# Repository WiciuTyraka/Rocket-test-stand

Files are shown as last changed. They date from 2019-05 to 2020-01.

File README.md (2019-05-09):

# Rocket test stand

## About
This is a project of rocket test stand to measure the trust and temperature of the engine and to save the data on SD-card. In nearly future I will add a wireless communication with computer to collect and proces data in real time. To wireless communication i will use a LoRa module.

- [Rocket test stand](#rocket-test-stand)
  * [About](#about)
  *  [PCB](#pcb)
      - [Schema](#schema)
      - [Board](#board)
      - [Libraries](#libraries)
  * [Sensors](#sensors)
      - [SD-card](#sd-card)
      - [Load cell and HX711](#load-cell-and-hx711)
      - [Thermocouples and max6675](#thermocouples-and-max6675)
      - [LoRa module](#lora-module)
      - [Pin map](#pin-map)
  * [Code for arduino](#code-for-arduino)
  * [Code for STM32](#code-for-stm32)

## PCB
Circut board is designed in Eagle

### Schema
 Rocket test stend consist of two board.
 - First board is a shield for Arduino Uno or STM32 Nucelo board. On this board is located a adpter for SD-card, amplifire for load cell and thermometr, and also a LoRa module.<br/>
[schema of rocket test stand board](https://github.com/WiciuTyraka/Rocket-test-stand/blob/master/PCB/Schema/Rocekt_test_stand.sch)
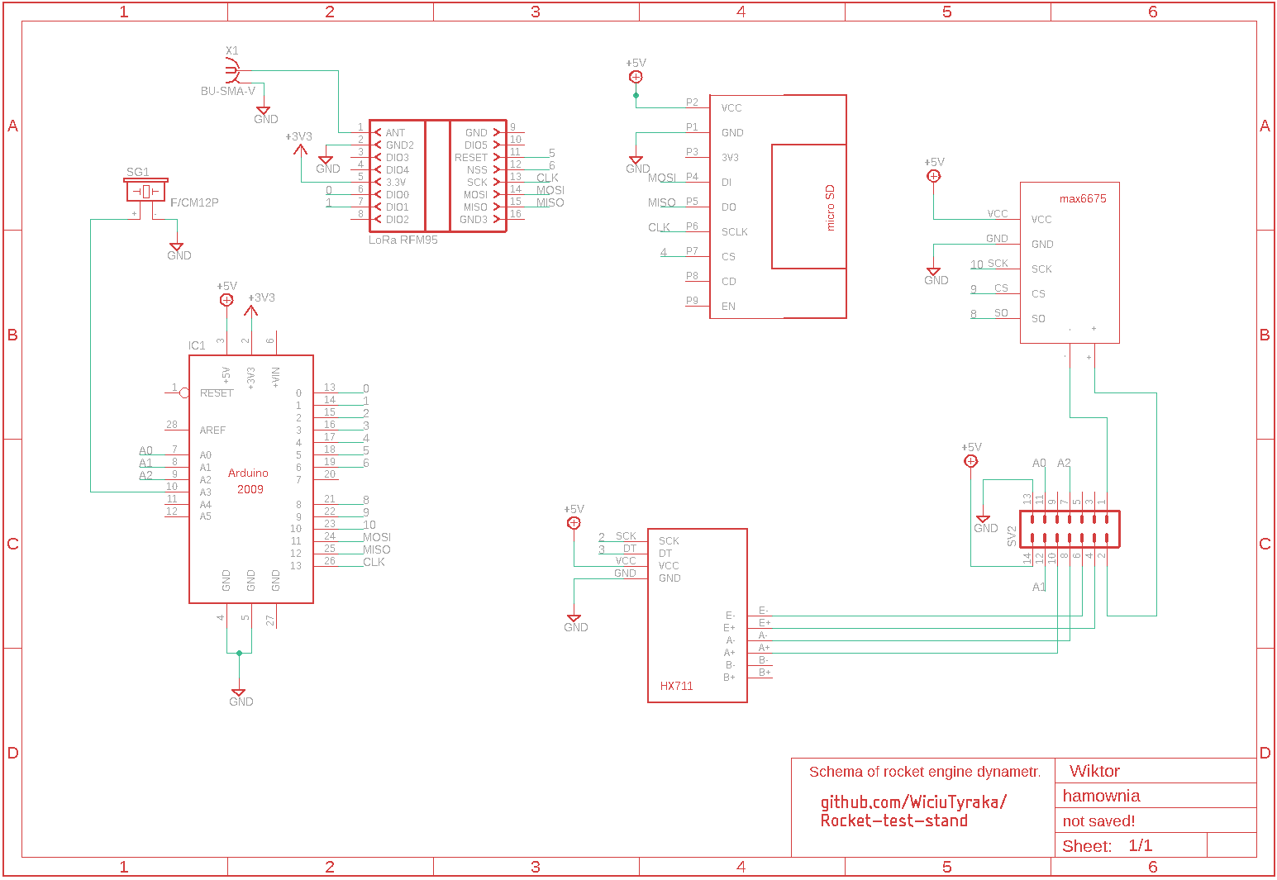
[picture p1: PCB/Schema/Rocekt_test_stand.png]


- Second board is used to collecting signals from sensors and ignite the engine.<br/>
[schema of input rocket test stand board](https://github.com/WiciuTyraka/Rocket-test-stand/blob/master/PCB/Schema/Rocekt_test_stand_input.sch)
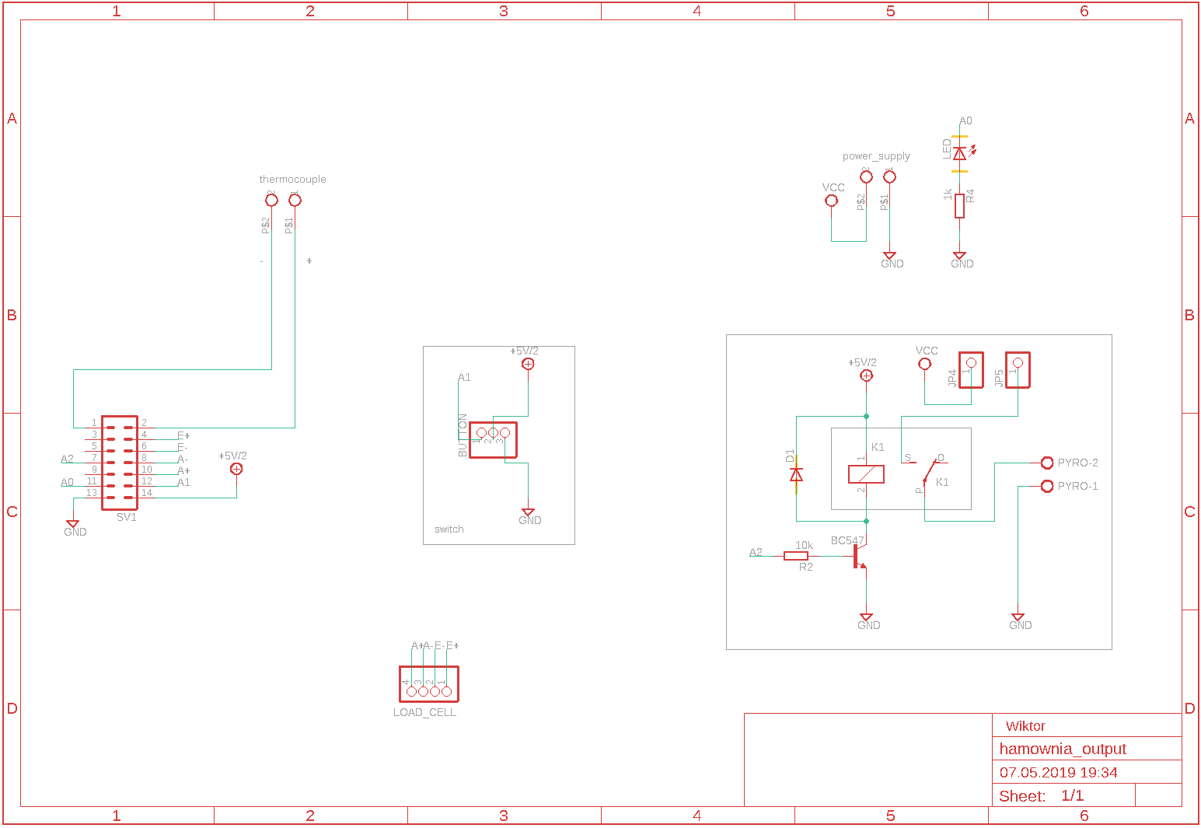
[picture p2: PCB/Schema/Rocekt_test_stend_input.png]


### Board
links for downloading a board file.
- [link for rocket_test_stend.brd](https://github.com/WiciuTyraka/Rocket-test-stand/blob/master/PCB/Board/Rocekt_test_stand.brd)
- [link for rocket_test_stend_input.brd](https://github.com/WiciuTyraka/Rocket-test-stand/blob/master/PCB/Board/Rocekt_test_stand_input.brd)

### Libraries
Here are a necessary libraries for elements thats are used in project.
- [ark 8.5mm](https://github.com/WiciuTyraka/Rocket-test-stand/blob/master/PCB/Lib/111_ark_8.5mm.lbr)
- [hx711](https://github.com/WiciuTyraka/Rocket-test-stand/blob/master/PCB/Lib/111_hx711.lbr)
- [LoRa module](https://github.com/WiciuTyraka/Rocket-test-stand/blob/master/PCB/Lib/111_LORA.lbr)
- [max6675](https://github.com/WiciuTyraka/Rocket-test-stand/blob/master/PCB/Lib/111_max6675.lbr)
- [microsd](https://github.com/WiciuTyraka/Rocket-test-stand/blob/master/PCB/Lib/111_microsd.lbr)

## Sensors
In this project are used few sensors and device, here you can find a exemple code, libraries and datasheet for them.

### SD-card
---
Micro sd-card adapter is used for saving all data in txt file or as a json.
<details>
<summary>details</summary>
</br>

#### Wireing schema
This is the schema for all the wireing with arduino
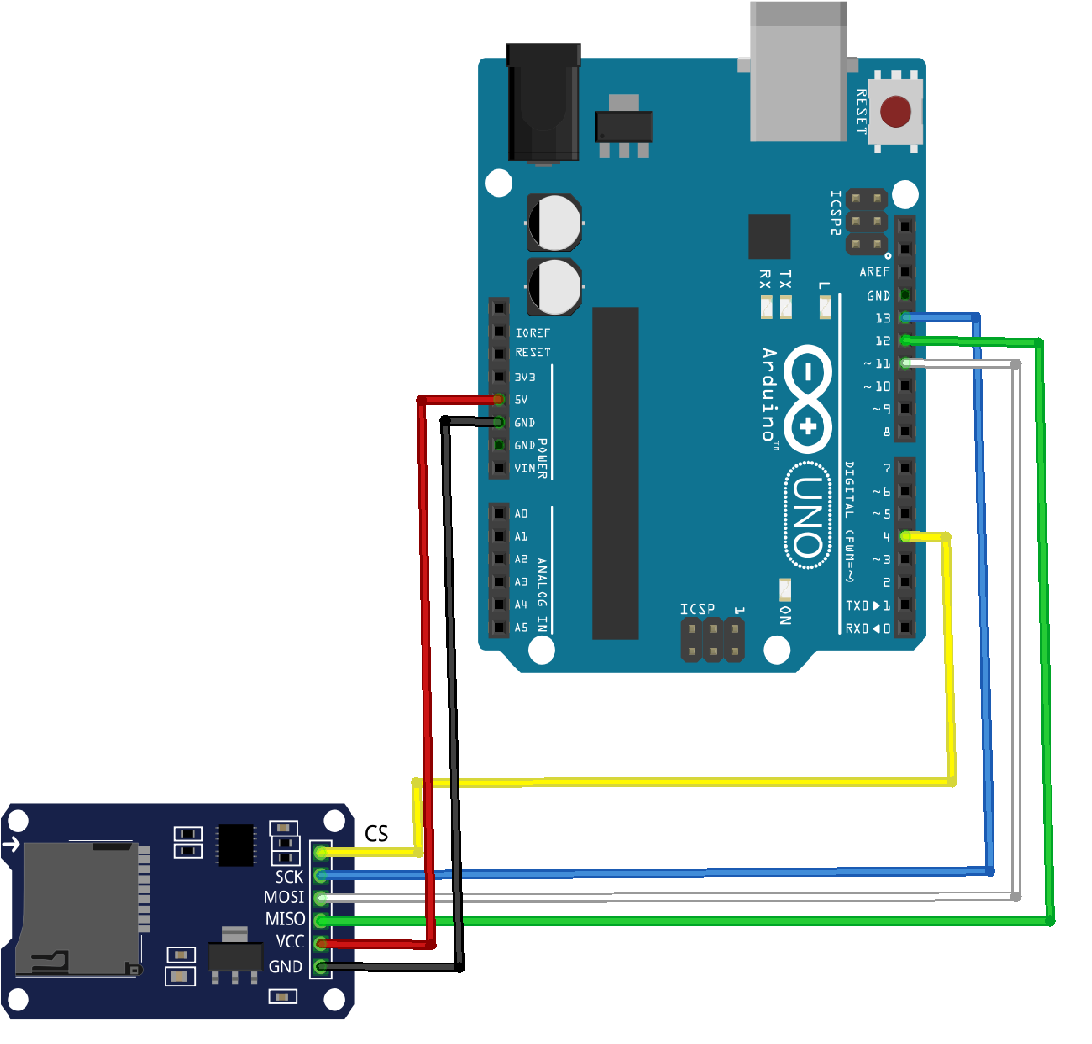
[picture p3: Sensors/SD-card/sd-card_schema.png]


#### Adapter wireing
| MicroSD Card Adapter | Adruino UNO Pin |
|---|---:|
| CS | 4 |
| SCK | 13 |
| MOSI | 11 |
| MISO | 12 |
| VCC | 5V |
| GND | GND |

#### Arduino code
[the necessary code is here](https://github.com/WiciuTyraka/Rocket-test-stand/blob/master/Sensors/SD-card/save_to_file/save_to_file.ino)
</details>

### Load cell and HX711
---
Load cell id used for measuring a engine thrust. Analog signal form load cell is converting to digital by HX711 amplifier
<details>
<summary>details</summary>
</br>
I cant find a datasheet for my chinese load cell so made this table

#### Basic load resistance checks
| Resistance check | Typical 350 Ω |
|---|---:|
| Ex+ to Ex- | ~410Ω |
| S+ to S- | 350Ω |
| Ex+ to S+ | ~315Ω |
| Ex+ to S- | ~315Ω |
| Ex- to S+ | ~280Ω |
| Ex- to S- | ~280Ω |

#### Load cell wireing
| HX711 | Load cell |
|---|---:|
| E+ | white |
| E- | red |
| S+ | black |
| S- | green |

#### Amplifer schema
This is a schema for all the wireing with arduino
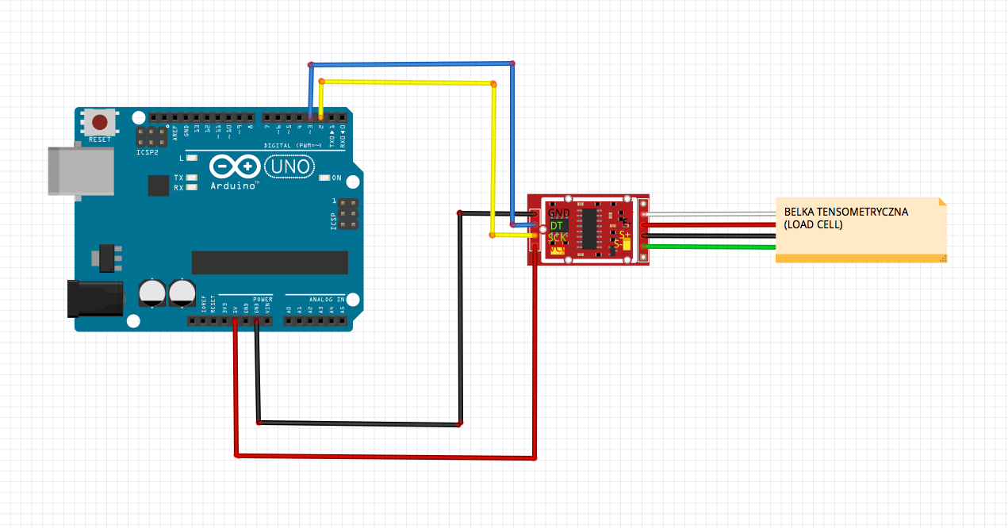
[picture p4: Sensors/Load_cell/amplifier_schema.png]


#### HX711 library
You can download the necessary library here:
[download](https://halckemy.s3.amazonaws.com/uploads/attachments/392655/HX711-master.zip)

#### Arduino code
All the code necessary for calibration the load cell and measuring the force:
- calibration:
[the code is here](https://github.com/WiciuTyraka/Rocket-test-stand/blob/master/Sensors/Load_cell/calibration/calibration.ino)
- measurment:
[the code is here](https://github.com/WiciuTyraka/Rocket-test-stand/blob/master/Sensors/Load_cell/measurment/measurment.ino)

#### Datasheet
[link](https://circuits4you.com/wp-content/uploads/2016/11/hx711_datasheet_english.pdf)
</details>

### Thermocouples and max6675
---
To measure a temperature of the combustion chember and nozzle I'm using a thermocouple. Analog signal from this sensor is converting to digital by max6675 amplifier

<details>
<summary>details</summary>
</br>

#### Specifications of max6675
| | |
|---|---:|
| Suply Voltage | 3.3 to 5 VDC |
| Operating Current | ~50mA |
| Measurement Range | 0 - 1024^∘C |
| Measurement Resolution | +/- 0.25^∘C |
| Output | Uses SPI interface |
| Required sensor | K Thermocouple |

#### Thermocouples schema
This is the schema for all the wireing with arduino
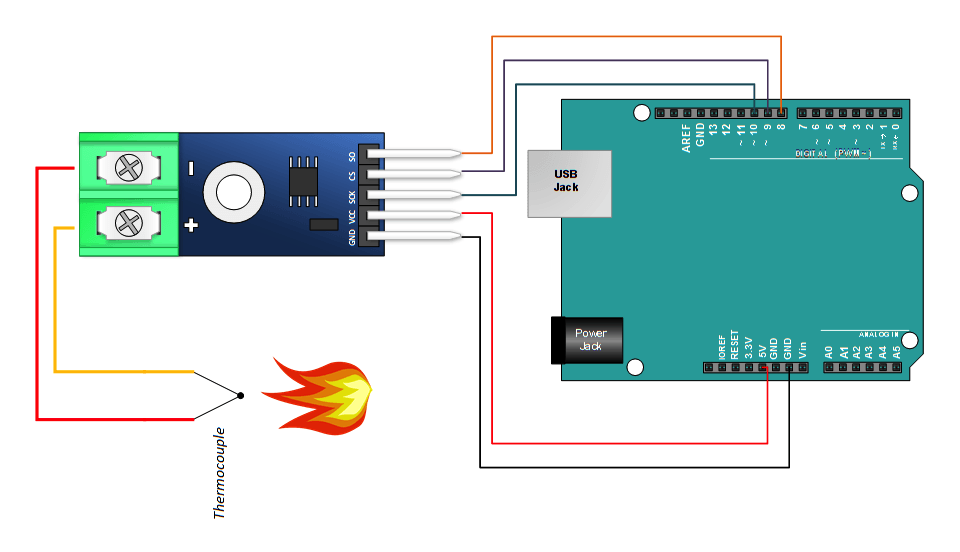
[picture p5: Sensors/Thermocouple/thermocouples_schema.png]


#### MAX6675 library
You can download the necessary library here:
[download](https://github.com/adafruit/MAX6675-library)

#### Arduino code
Basic code for reading temperature
[the necessary code is here](https://github.com/WiciuTyraka/Rocket-test-stand/blob/master/Sensors/Thermocouple/thermocouples/thermocouples.ino)

#### Datasheet
[link](http://henrysbench.capnfatz.com/wp-content/uploads/2015/05/MAX6675-Datasheet.pdf)

</details>

### LoRa module
---
I used LoRa transceiver to ignite the engine from safe distance also wireless communication allows me to watch data in real time.

<details>
<summary>details</summary>
</br>

The chip I used in project is a RFM95W transceiver.
The  RFM95W transceivers  feature  the  LoRaTM  long range modem that provides ultra-long range spread spectrum communication and high interference immunity whilst minimising current consumption.

#### RFM95W schema
This is the schema for all the wireing with arduino
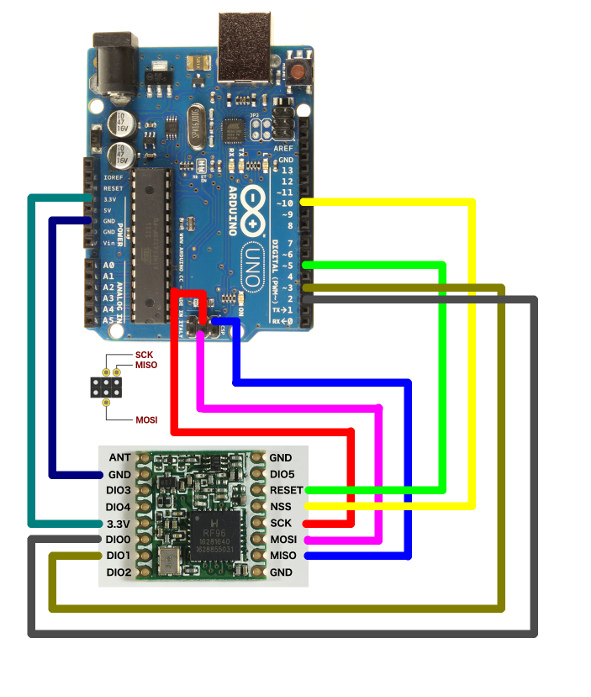
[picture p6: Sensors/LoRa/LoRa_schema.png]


#### RFM95W library
You can download the necessary library here:
[download](https://github.com/PaulStoffregen/RadioHead)

#### Arduino code
Here is a code for a transmiter and reciver(in fact both of them are transceivers) :
- transmiter:
[the code is here](https://github.com/WiciuTyraka/Rocket-test-stand/blob/master/Sensors/LoRa/transmiter/transmiter.ino)
- reciver:
[the code is here](https://github.com/WiciuTyraka/Rocket-test-stand/blob/master/Sensors/LoRa/reciver/reciver.ino)

#### Datasheet
[link](https://www.hoperf.com/modules/lora/RFM95.html)

</details>

### Pin map
---
This table contains information abaout all pins to witch are connected device

| Pin number |Device |
|---|--- |
| 0 |LoRa DIO0  |
| 1 |LoRa DIO1  |
| 2 |HX711 CLK  |
| 3 |HX711 DOUT |
| 4 |SD card |
| 5 |LoRa RESET |
| 6 |LoRa CS |
| 8 |max6675 CS |
| 9 |max6675 SO |
| 10 |max6675 SCK|
| 11 |MOSI |
| 12 |MISO |
| 13 |CLK |
| 14 |switch |
| 15 |led |
| 16 |ignite |
| 17 |buzzer |

## Code for Arduino

This version of code not include a wireless communication
- here you can find a [code](https://github.com/WiciuTyraka/Rocket-test-stand/blob/master/Arduino_code/Rocekt_test_stand/Rocekt_test_stand.ino)

## Code for STM32
cause i'm very busy right now, i'll back to this task in nearly future.

*by* Wiktor Tasarek

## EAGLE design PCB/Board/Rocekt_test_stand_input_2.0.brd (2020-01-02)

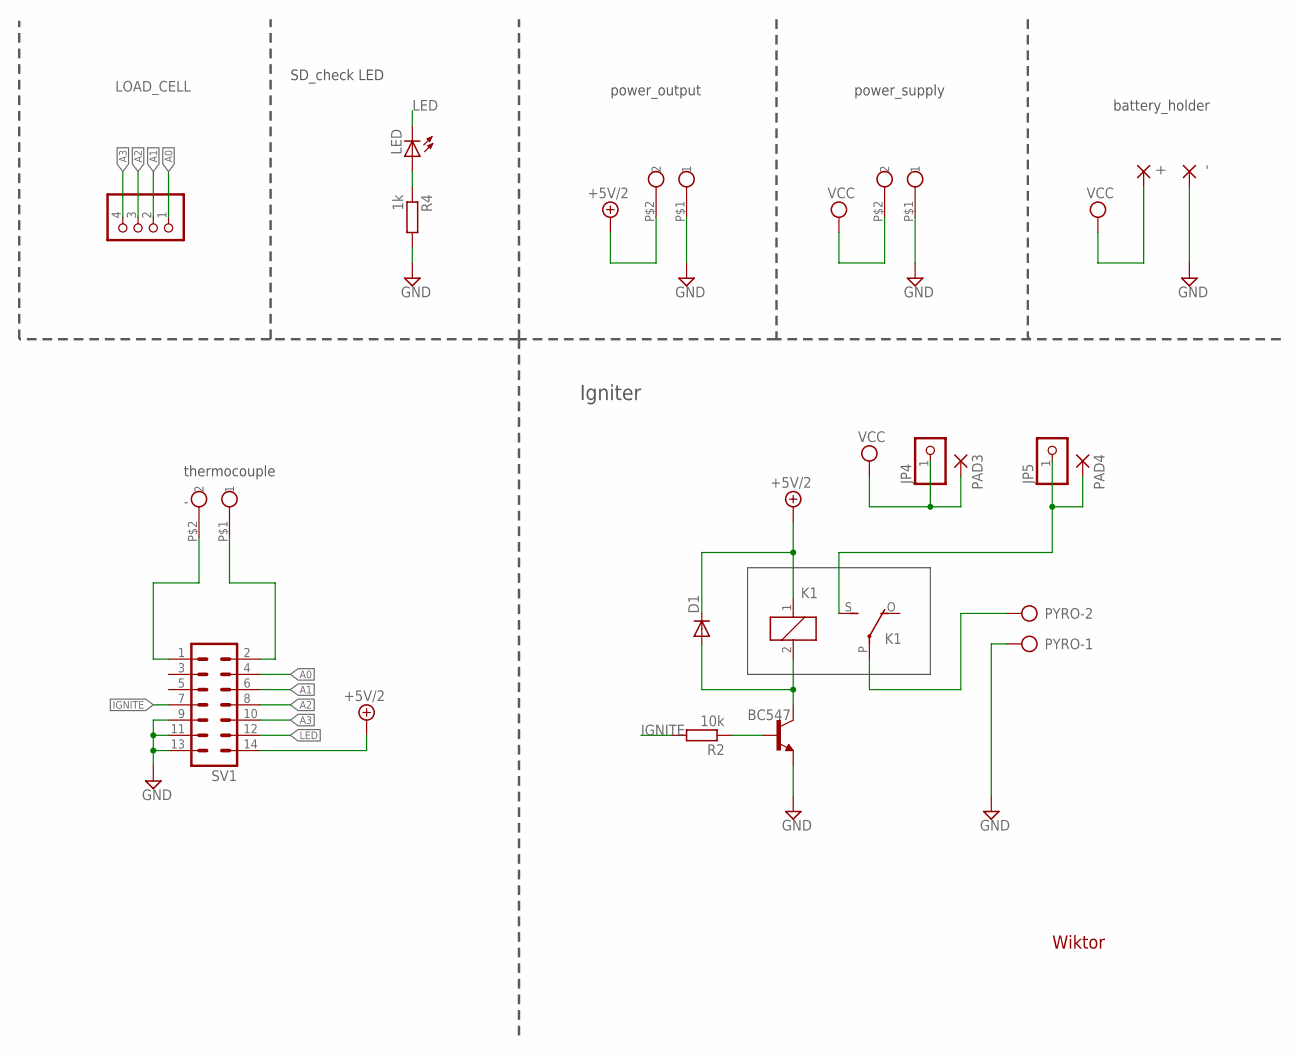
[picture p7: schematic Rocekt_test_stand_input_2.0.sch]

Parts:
+: SMD5; SMD2,54-5,08
-: SMD5; SMD2,54-5,08
D1: 1N4004; DO41-10
JP4, JP5: PINHD-1X1; 1X01
K1: G5L; G5LE
LED: LED_ELD260; LED_LD260
LOAD_CELL: PINHD-1X4; 1X04
PAD3, PAD4: SMD2; SMD1,27-2,54
POWER_SUPPLY, POWER_SUPPLY1: ARK_8.5MM; ZLACZESRUBOWE8.5MM
PYRO: AK500/2
R2: 10k; 0204/5
R4: 1k; 0204/5
SV1: ML14
T1: BC547; TO92
U$1: ARK_8.5MM; ZLACZESRUBOWE8.5MM

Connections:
+5V/2: D1.C, K1.1, POWER_SUPPLY1.P$2 (2), SV1.14
-: SV1.1, U$1.P$2 (2)
A0: LOAD_CELL.1, SV1.4
A1: LOAD_CELL.2, SV1.6
A2: LOAD_CELL.3, SV1.8
A3: LOAD_CELL.4, SV1.10
GND: -.1, POWER_SUPPLY.P$1 (1), POWER_SUPPLY1.P$1 (1), PYRO.1, R4.2, SV1.9, SV1.11, SV1.13, T1.1 (E)
IGNITE: R2.2, SV1.7
LED: LED.K (C), SV1.12
unnamed: D1.A, K1.2, T1.3 (C)
unnamed: R2.1, T1.2 (B)
unnamed: K1.P, PYRO.2
unnamed: SV1.2, U$1.P$1 (1)
unnamed: LED.A, R4.1
unnamed: JP5.1, K1.S, PAD4.1
VCC: +.1, JP4.1, PAD3.1, POWER_SUPPLY.P$2 (2)

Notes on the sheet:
thermocouple
power_supply
Wiktor
battery_holder
power_output
SD_check LED
Igniter

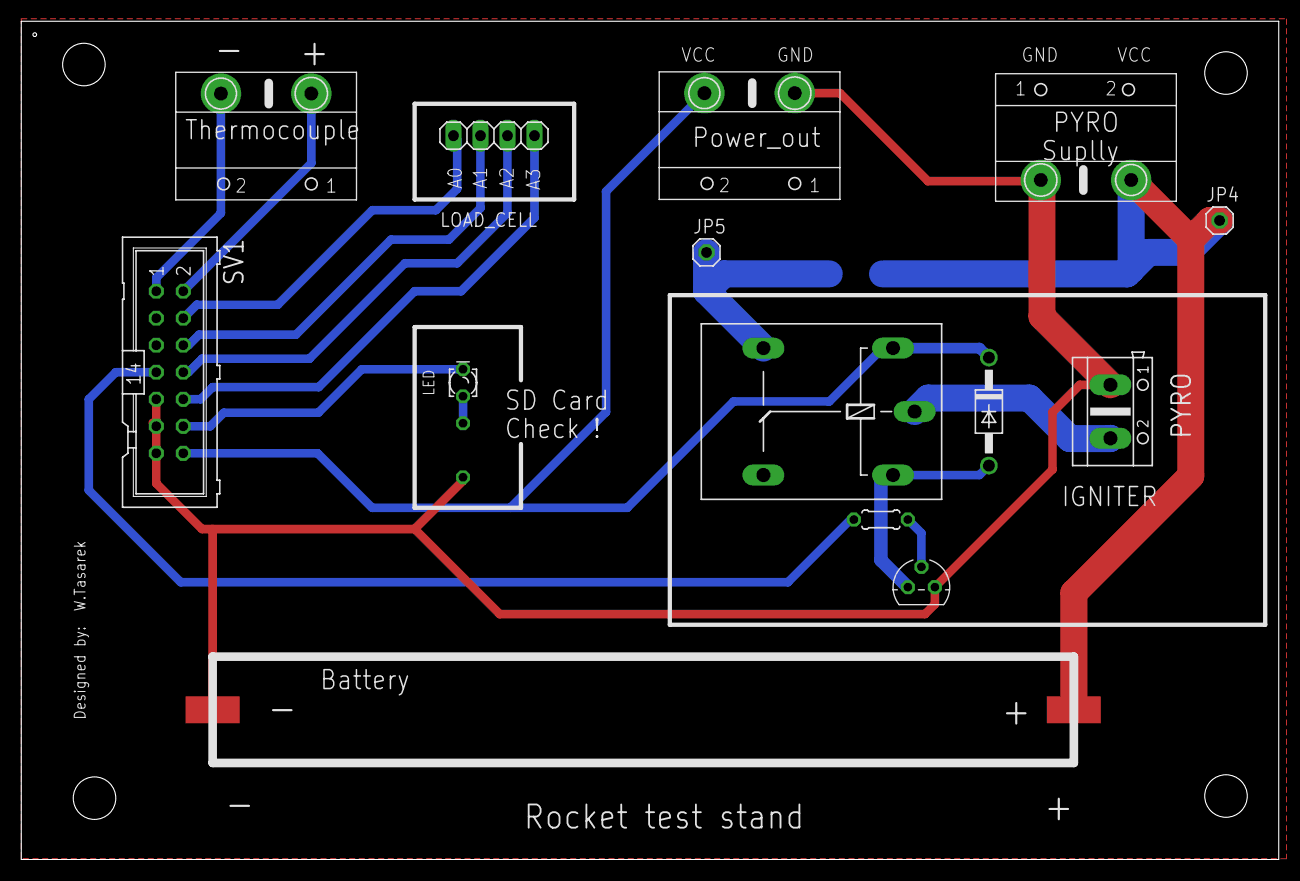
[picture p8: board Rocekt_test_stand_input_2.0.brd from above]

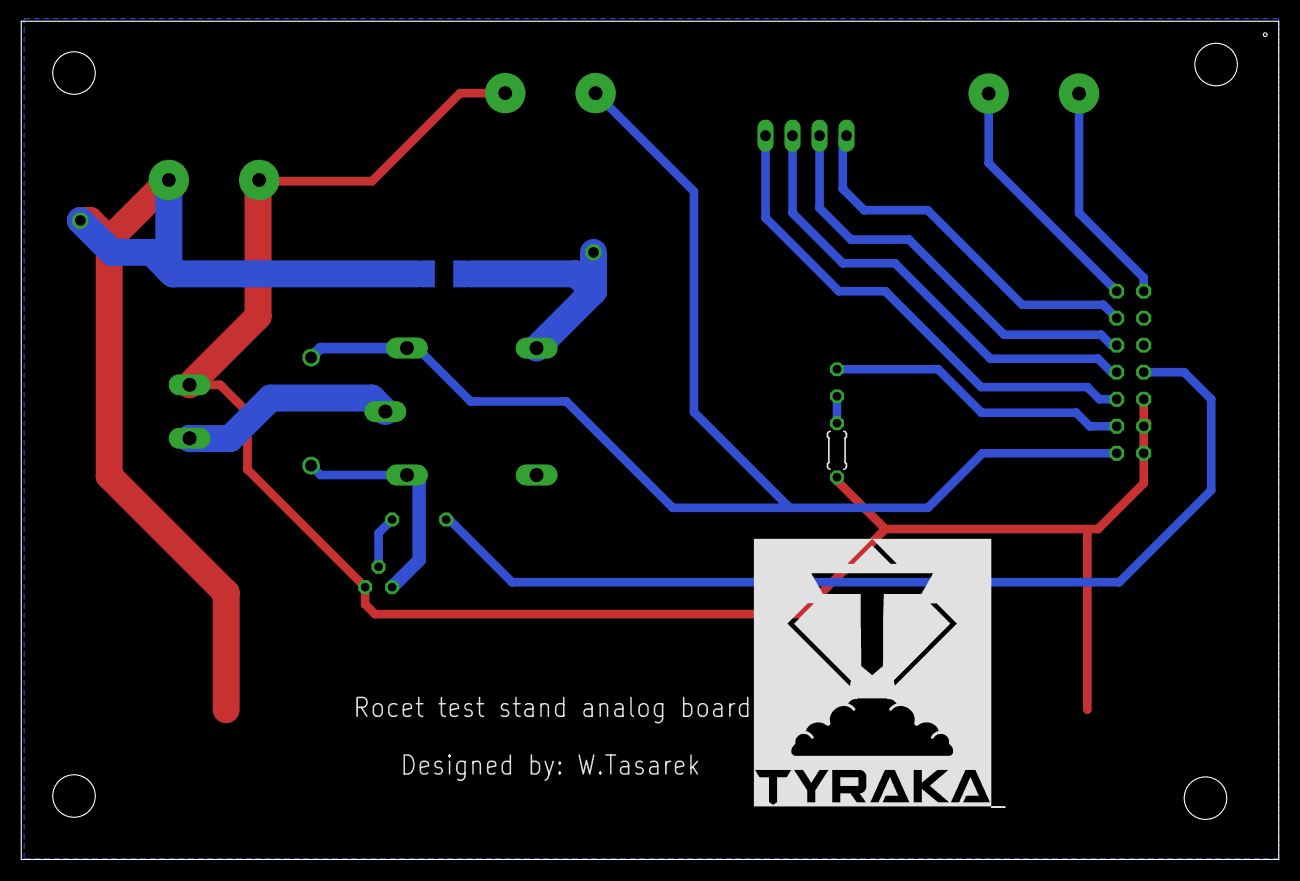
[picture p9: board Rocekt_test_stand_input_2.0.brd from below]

Board: 2 copper layers, 118.3 x 78.8 mm, 18 parts (3 on the bottom side), 16 nets.

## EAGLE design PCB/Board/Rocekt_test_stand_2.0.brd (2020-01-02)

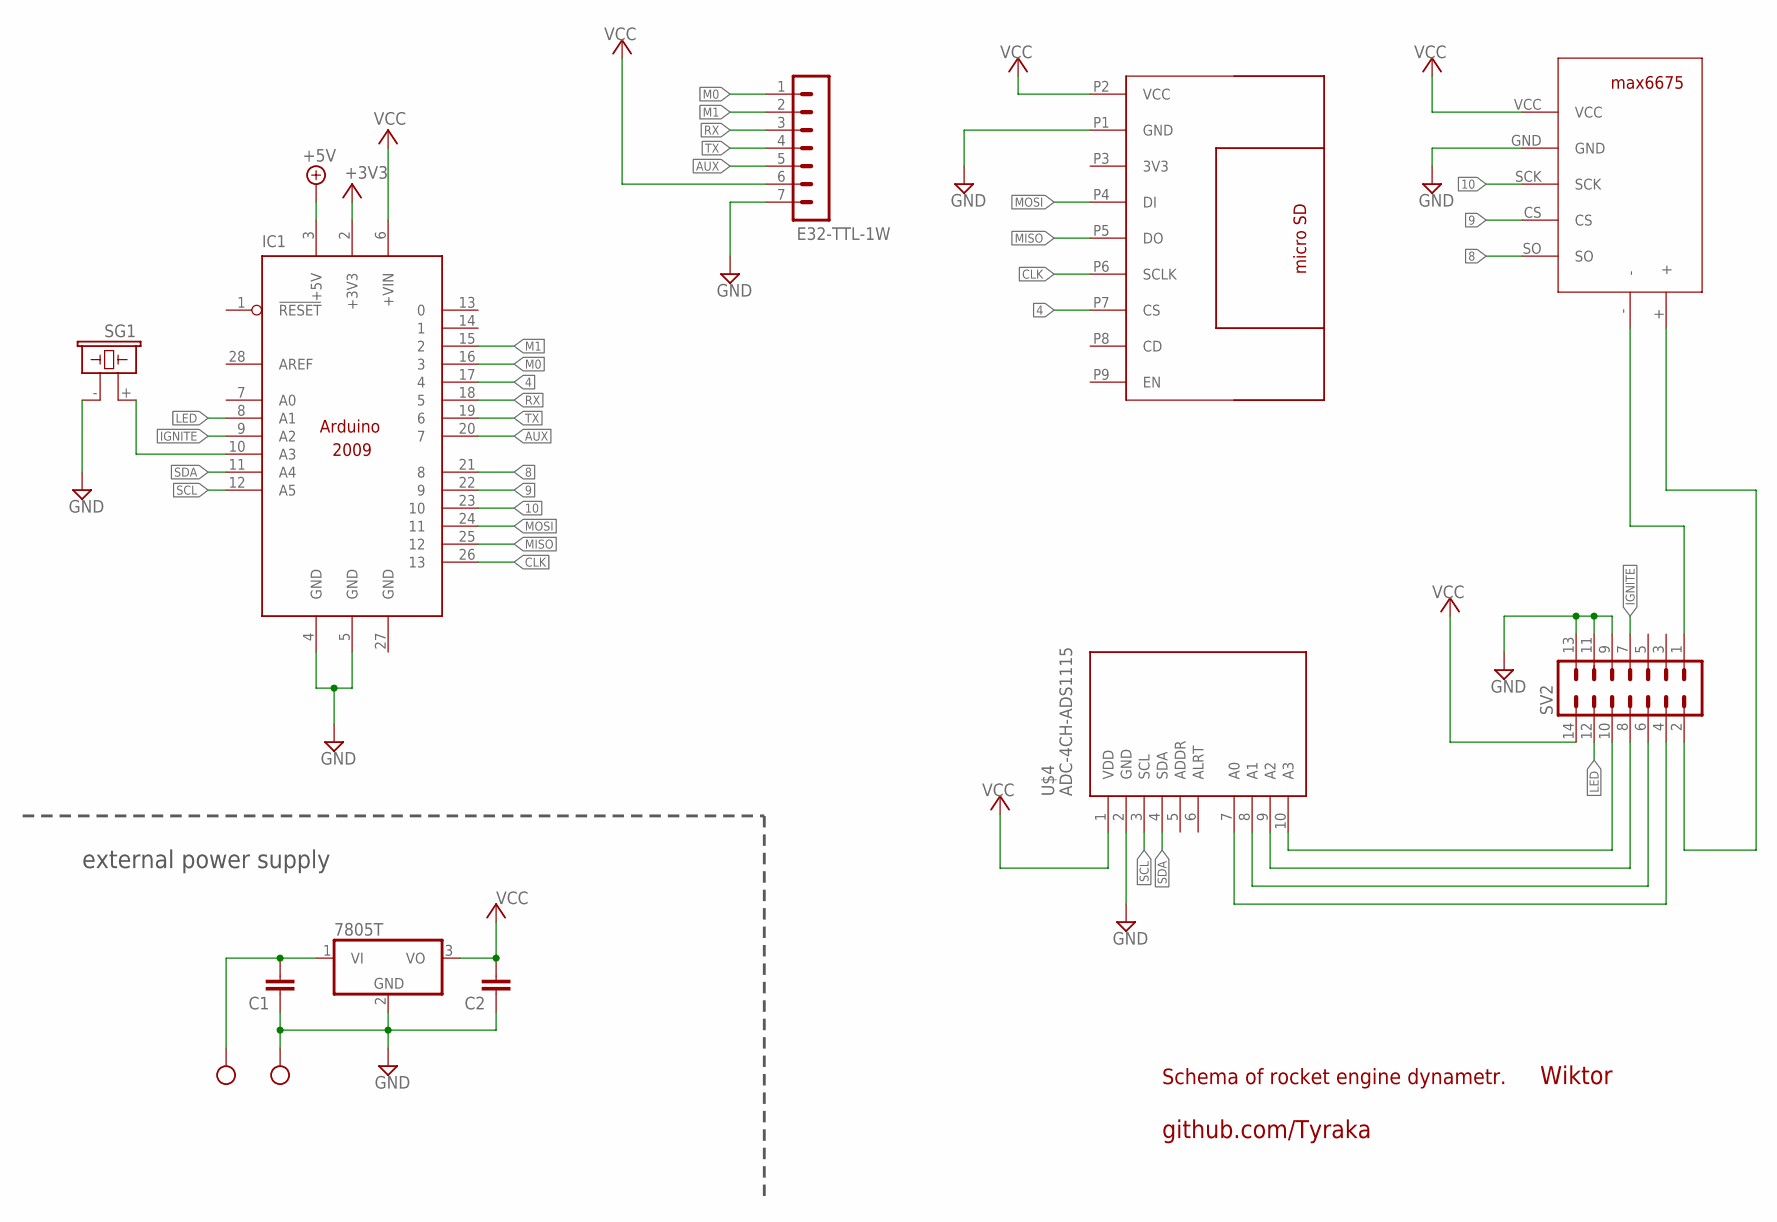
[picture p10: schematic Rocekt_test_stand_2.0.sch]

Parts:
C1, C2: C2.5/4; C2.5-4
E32-TTL-1W: MA07-1
IC1: ARDUINO2009_10; ARDUINO2009
IC2: 7805T; TO220H
SD1: MICRO_SD
SG1: F/CM12P
SV2: ML14
U$2: MAX6675; MAX6675_FOOTPRINT
U$4: ADC-4CH-ADS1115
X1: AK300/2

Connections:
4: IC1.17 (4), SD1.P7 (CS)
8: IC1.21 (8), U$2.SO
9: IC1.22 (9), U$2.CS
10: IC1.23 (10), U$2.SCK
+3V3: IC1.2 (+3V3)
+5V: IC1.3 (+5V)
AUX: E32-TTL-1W.5, IC1.20 (7)
CLK: IC1.26 (13), SD1.P6 (SCLK)
GND: C1.1, C2.1, E32-TTL-1W.7, IC1.4 (GND), IC1.5 (GND), IC1.27 (GND), IC2.2 (GND), SD1.P1 (GND), SG1.- (2), SV2.9, SV2.11, SV2.13, U$2.GND, U$4.2 (GND), X1.2
IGNITE: IC1.9 (A2), SV2.7
LED: IC1.8 (A1), SV2.12
M0: E32-TTL-1W.1, IC1.16 (3)
M1: E32-TTL-1W.2, IC1.15 (2)
MISO: IC1.25 (12), SD1.P5 (DO)
MOSI: IC1.24 (11), SD1.P4 (DI)
unnamed: SV2.2, U$2.+
unnamed: IC1.10 (A3), SG1.+ (1)
unnamed: SV2.1, U$2.-
unnamed: SV2.4, U$4.7 (A0)
unnamed: SV2.10, U$4.10 (A3)
unnamed: SV2.8, U$4.9 (A2)
unnamed: SV2.6, U$4.8 (A1)
unnamed: C1.2, IC2.1 (VI), X1.1
RX: E32-TTL-1W.3, IC1.18 (5)
SCL: IC1.12 (A5), U$4.3 (SCL)
SDA: IC1.11 (A4), U$4.4 (SDA)
TX: E32-TTL-1W.4, IC1.19 (6)
VCC: C2.2, E32-TTL-1W.6, IC1.6 (+VIN), IC2.3 (VO), SD1.P2 (VCC), SV2.14, U$2.VCC, U$4.1 (VDD)

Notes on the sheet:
Wiktor
Schema of rocket engine dynametr.
github.com/Tyraka
external power supply

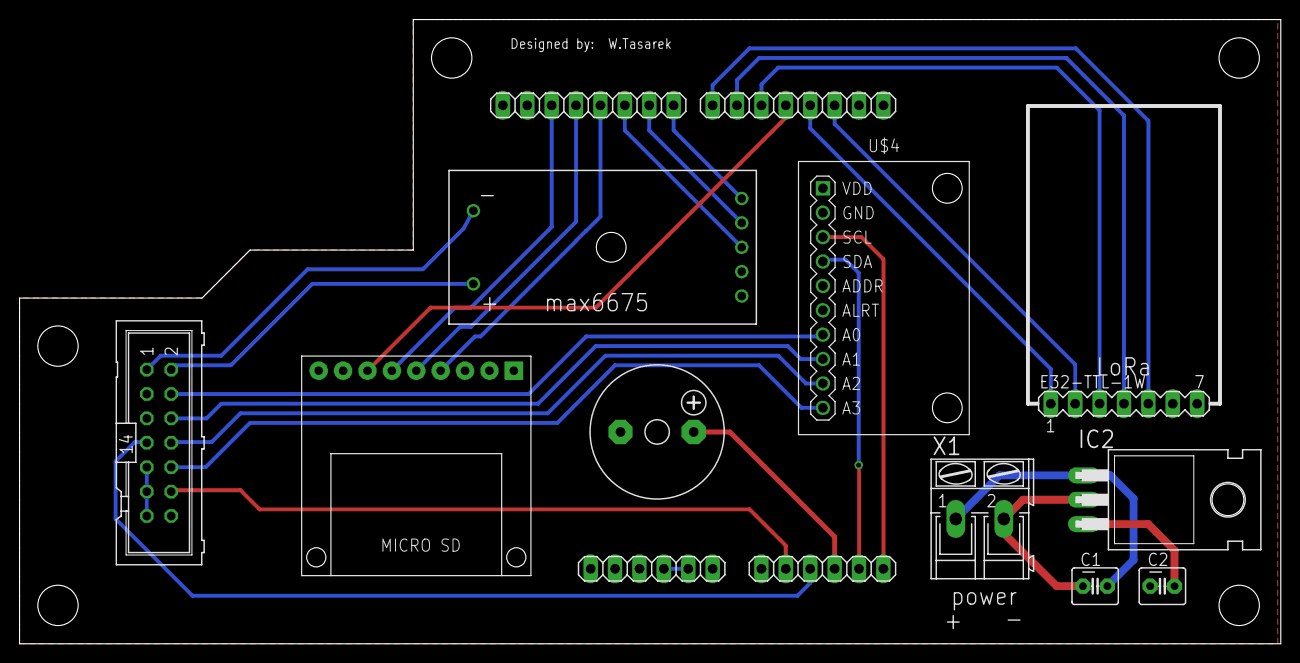
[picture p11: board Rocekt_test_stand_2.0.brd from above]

Board: 2 copper layers, 131.3 x 65.0 mm, 11 parts (0 on the bottom side), 26 nets.

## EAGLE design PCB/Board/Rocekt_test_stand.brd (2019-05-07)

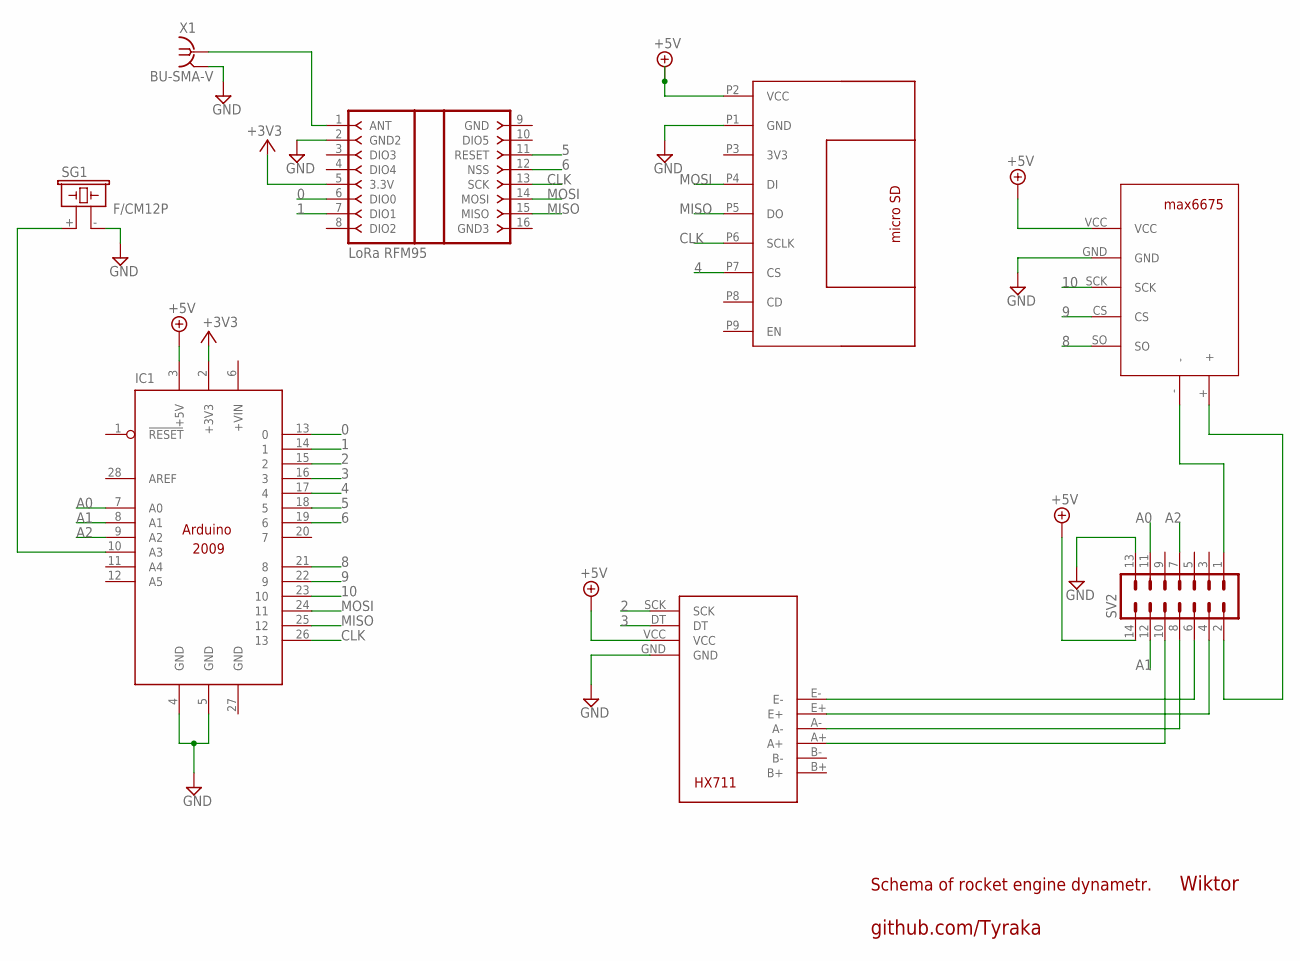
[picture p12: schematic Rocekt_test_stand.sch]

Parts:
IC1: ARDUINO2009_10; ARDUINO2009
LORA: LORA_RFM95_ADAPTERLORA_RFM95W; LORA_RFM95_ADAPTER
SD1: MICRO_SD
SG1: F/CM12P
SV2: ML14
U$1: HX711
U$2: MAX6675; MAX6675_FOOTPRINT
X1: BU-SMA-V

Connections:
0: IC1.13 (0), LORA.6 (DIO0)
1: IC1.14 (1), LORA.7 (DIO1)
2: IC1.15 (2), U$1.SCK
3: IC1.16 (3), U$1.DT
4: IC1.17 (4), SD1.P7 (CS)
5: IC1.18 (5), LORA.11 (RESET)
6: IC1.19 (6), LORA.12 (NSS)
8: IC1.21 (8), U$2.SO
9: IC1.22 (9), U$2.CS
10: IC1.23 (10), U$2.SCK
+3V3: IC1.2 (+3V3), LORA.5 (3.3V)
+5V: IC1.3 (+5V), SD1.P2 (VCC), SV2.14, U$1.VCC, U$2.VCC
A0: IC1.7 (A0), SV2.11
A1: IC1.8 (A1), SV2.12
A2: IC1.9 (A2), SV2.7
CLK: IC1.26 (13), LORA.13 (SCK), SD1.P6 (SCLK)
GND: IC1.4 (GND), IC1.5 (GND), IC1.27 (GND), LORA.2 (GND2), SD1.P1 (GND), SG1.- (2), SV2.13, U$1.GND, U$2.GND, X1.2, X1.3 (2), X1.4 (2), X1.5 (2)
MISO: IC1.25 (12), LORA.15 (MISO), SD1.P5 (DO)
MOSI: IC1.24 (11), LORA.14 (MOSI), SD1.P4 (DI)
unnamed: SV2.2, U$2.+
unnamed: IC1.10 (A3), SG1.+ (1)
unnamed: SV2.1, U$2.-
unnamed: SV2.4, U$1.E+
unnamed: SV2.6, U$1.E-
unnamed: SV2.8, U$1.A-
unnamed: LORA.1 (ANT), X1.1
unnamed: SV2.10, U$1.A+

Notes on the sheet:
Wiktor
Schema of rocket engine dynametr.
github.com/Tyraka

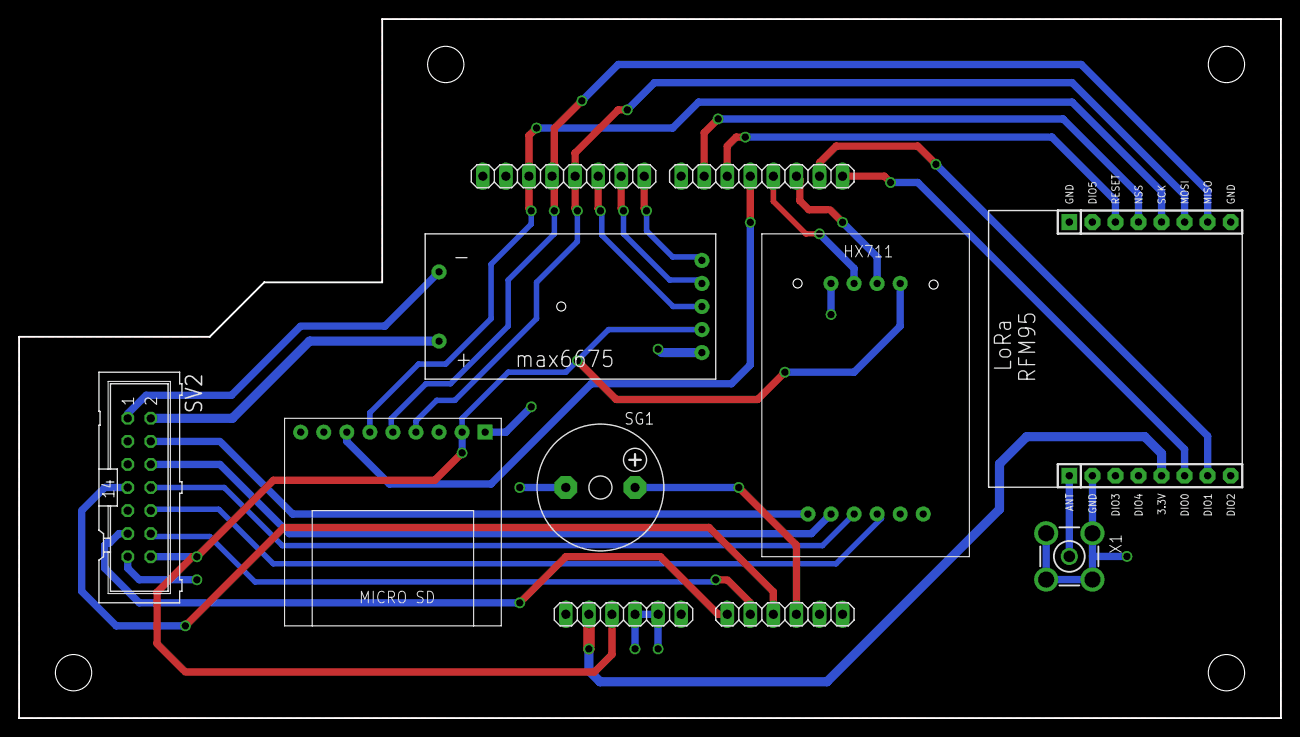
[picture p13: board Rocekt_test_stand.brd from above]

Board: 2 copper layers, 139.0 x 77.0 mm, 8 parts (0 on the bottom side), 27 nets.

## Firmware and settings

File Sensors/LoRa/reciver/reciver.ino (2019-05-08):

// Arduino9x_RX
// -*- mode: C++ -*-
// Example sketch showing how to create a simple messaging client (receiver)
// with the RH_RF95 class. RH_RF95 class does not provide for addressing or
// reliability, so you should only use RH_RF95 if you do not need the higher
// level messaging abilities.
// It is designed to work with the other example Arduino9x_TX

#include <SPI.h>
#include <RH_RF95.h>

#define RFM95_CS 10
#define RFM95_RST 0
#define RFM95_INT 2

// Change to 434.0 or other frequency, must match RX's freq!
#define RF95_FREQ 868.0

// Singleton instance of the radio driver
RH_RF95 rf95(RFM95_CS, RFM95_INT);

// Blinky on receipt
#define LED 13

void setup() 
{
  pinMode(LED, OUTPUT);     
  pinMode(RFM95_RST, OUTPUT);
  digitalWrite(RFM95_RST, HIGH);

  while (!Serial);
  Serial.begin(9600);
  delay(100);

  Serial.println("Arduino LoRa RX Test!");
  
  // manual reset
  digitalWrite(RFM95_RST, LOW);
  delay(10);
  digitalWrite(RFM95_RST, HIGH);
  delay(10);

  while (!rf95.init()) {
    Serial.println("LoRa radio init failed");
    while (1);
  }
  Serial.println("LoRa radio init OK!");

  // Defaults after init are 434.0MHz, modulation GFSK_Rb250Fd250, +13dbM
  if (!rf95.setFrequency(RF95_FREQ)) {
    Serial.println("setFrequency failed");
    while (1);
  }
  Serial.print("Set Freq to: "); Serial.println(RF95_FREQ);

  // Defaults after init are 434.0MHz, 13dBm, Bw = 125 kHz, Cr = 4/5, Sf = 128chips/symbol, CRC on

  // The default transmitter power is 13dBm, using PA_BOOST.
  // If you are using RFM95/96/97/98 modules which uses the PA_BOOST transmitter pin, then 
  // you can set transmitter powers from 5 to 23 dBm:
  rf95.setTxPower(23, false);
}

void loop()
{
  if (rf95.available())
  {
    // Should be a message for us now   
    uint8_t buf[RH_RF95_MAX_MESSAGE_LEN];
    uint8_t len = sizeof(buf);
    
    if (rf95.recv(buf, &len))
    {
      digitalWrite(LED, HIGH);
      RH_RF95::printBuffer("Received: ", buf, len);
      Serial.print("Got: ");
      Serial.println((char*)buf);
       Serial.print("RSSI: ");
      Serial.println(rf95.lastRssi(), DEC);
      
      // Send a reply
      uint8_t data[] = "And hello back to you";
      rf95.send(data, sizeof(data));
      rf95.waitPacketSent();
      Serial.println("Sent a reply");
      digitalWrite(LED, LOW);
       digitalWrite(RFM95_RST, LOW);
     delay(10);
     digitalWrite(RFM95_RST, HIGH);
      delay(10);
    }
    else
    {
      Serial.println("Receive failed");
    }
  }
}

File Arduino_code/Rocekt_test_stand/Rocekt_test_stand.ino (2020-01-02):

#include <Arduino.h>
#include <SPI.h>
#include <SD.h>                                    // biblioteka do karty SD
#include "HX711.h"                                 // biblioteka do hamowni

#define DOUT  3
#define CLK  2
#define LED 15
#define PYRO 16
#define BUZZER 17

///////////////////   --------------   SETTING !!!   -----------------    ///////////////////////////

#define CALIB_FACTOR 9600   // <----------- tu musisz wpisac wspolczynnik kalibracji

#define TIME_FOR_RUN 5000      // czas na ucieczke liczony w [ms]

#define FIRE 5000             // czas przez ktorey bedzie sie palic grzala w [ms]

//////////////////------------------------------------------------------------/////////////////////////////

HX711 scale(DOUT, CLK);
File plik;

int temp_time = 0;
float trust = 0;


void logger(float);

void setup()
{
  Serial.begin(56650);                                    //uruchom UART o prędkości 9600 baud

  pinMode(LED, OUTPUT);                   // definicja leda
  digitalWrite(LED, LOW);                 // led wylaczony

  pinMode(PYRO, OUTPUT);                  //definicja zapalnika
  digitalWrite(PYRO, LOW);                //zapalnik wylaczony

  pinMode(BUZZER, OUTPUT);               //definicja buzzera

  scale.set_scale(CALIB_FACTOR);                       // ustawienie wspolczynnika kalibracji
  scale.tare();                                        //taruj wage

  Serial.begin(9600);                                    //uruchom UART o prędkości 9600 baud



  if (!SD.begin(4))                                       //sprawdź czy nie ma karty na pinie ChipSelect 4
  {
     Serial.println("Nie wykryto karty(ERR)");            //błąd wykrycia karty
     while(1);                                              // zatrzymaj program
  }

  Serial.println("Karta Wykryta (3/3))");                 //Karta wykryta
  digitalWrite(LED, HIGH);

  if (SD.exists("readouts.txt"))                               //sprawdź czy istnieje plik o nazwie readouts.txt
  {

   Serial.println("Plik o podanej nazwie istnieje !");

  }

  else                                                   //jeżeli nie istnieje to
  {

   plik = SD.open("readouts.txt", FILE_WRITE);                //utwórz plik
   Serial.println("Utworzono plik o nazwie readouts.txt");

  }
  //delay(3000);

  while(millis() < TIME_FOR_RUN)
  {
     tone(17, 2000,500);      // wlacz buzzer na 0.5s
     delay(1000);

  }

  temp_time = millis();
  digitalWrite(PYRO,HIGH);
}


void loop()
{
  if((millis() - temp_time) > FIRE)
  {
    digitalWrite(PYRO,LOW);
  }

  trust = scale.get_units();
  Serial.print("trust: ");
  Serial.print(trust);
  Serial.println(" N");
  Serial.println();


  logger(trust);                            //zapisz na karte

}

void logger(float trust)
{

  plik = SD.open("readouts.txt", FILE_WRITE);                   //otwórz plik readouts.txt
  plik.println(trust);                                         //zapisz dane
  plik.close();                                            //zamknij/zapisz plik
  delay(150);
  Serial.println("Zapisano !");                            //poinformuj o zapisaniu pliku

}

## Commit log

2019-05-07 pcb menu
2019-05-08 pin map
2019-05-08 add lib and arduino code
2019-05-08 arduino code
2019-05-08 board fix
    [Rocekt_test_stand.brd, Rocekt_test_stand.sch, Rocekt_test_stand_input.brd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]
2019-05-09 menu fix
    [hamownia.sch]
2019-05-09 pin map add
2020-01-02 plytki na inynierke
    plytki na inzynierke
    [Rocekt_test_stand_2.0.brd, Rocekt_test_stand_2.0.sch, Rocekt_test_stand_input_2.0.brd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]

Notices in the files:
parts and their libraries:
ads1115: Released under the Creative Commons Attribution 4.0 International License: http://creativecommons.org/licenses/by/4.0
